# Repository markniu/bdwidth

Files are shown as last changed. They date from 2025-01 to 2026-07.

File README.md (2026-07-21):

# Filament monitor Sensor bdwidth

- Through the generated CSV file, we can intuitively see the diameter of the entire filament roll in the line chart in any position
- Improve print quality with automatic flow rate adjustment and stability with the runout/clog feature.

#### bdwidth sensor is an optical width and motion sensor for 3D printer.
I developed a unique algorithm that uses light diffraction to automatically compensate for filament shadows on the CCD sensor, even when the filament moves at different distances and angles, we still can get the right width.

  Just power it, then you can measure your filament motion&diameter.  



1. Flow compensation:  adjust the flow rate in real time

2. Jam/Runout: Pause the printer while jam or runout (laser optical tracking chip)
 
3. Width Accuracy: +/- 0.015mm  
 
4. Connection: USB or I2C, Low power 5V*49mA = 0.245W

5. No calibration required

6. firmware update from the usb (Only needs updating when we release a new bdwidth.hex)
   
7. No mechanical contact with the filament, no wear due to the use of optical components

[flow adjust](https://static.wixstatic.com/media/0d0edf_dd1a7dbbf0d7433387d54fea9a8ac6f3~mv2.jpg/v1/fill/w_1486,h_753,al_c,q_85,usm_0.66_1.00_0.01/0d0edf_dd1a7dbbf0d7433387d54fea9a8ac6f3~mv2.jpg)

[filament actual used](https://static.wixstatic.com/media/0d0edf_f45dd0ee38ac41dd8bb5706e1e4dc5ea~mv2.jpg/v1/fill/w_1440,h_753,al_c,q_85,usm_0.66_1.00_0.01/0d0edf_f45dd0ee38ac41dd8bb5706e1e4dc5ea~mv2.jpg)

[width chart](https://static.wixstatic.com/media/0d0edf_18b3c14cc95a42f3876c291456ff140b~mv2.jpg/v1/fill/w_1330,h_753,al_c,q_85,usm_0.66_1.00_0.01/0d0edf_18b3c14cc95a42f3876c291456ff140b~mv2.jpg)

## Quick start

#### 1.Plug the bdwidth sensor into the USB port or I2C port(it can be any two gpios) on the 3D printer mainboard 

#### 2.Install software module
```
cd  ~
git clone https://github.com/markniu/bdwidth.git
chmod 777 ~/bdwidth/klipper/install.sh
~/bdwidth/klipper/install.sh
```

#### 3.Configure Klipper

add the following section into your klipper config file,

here we connect the bdwidth to the usb port

```
[bdwidth fila_width_0]
port:usb
#   usb or i2c 
#i2c_software_scl_pin:PA8
#i2c_software_sda_pin:PA14
#   needed if the port is i2c
serial:/dev/serial/by-id/usb-1a86_USB_Serial-if00-port0
#serial:/dev/serial/by-path/YourByPathUUID
#   needed if the port is usb
# note: if you also have a bd_pressure , you must use  a serial: /dev/serial/by-path method.
# uncomment the above by-path line and replace the "YourByPathUUID" with the UUID for the bd_width. See the bd_pressure repository for instruction for bd_pressure. 
# It's best to start with both unplugged, then use command: ls /dev/serial/by-path and take note of the UUIDs with both unplugged.
# Repeat the command again after plugging in bd_width. Take note of the UUID for it, then again repeat for bd_pressure.

default_nominal_filament_diameter: 1.75 # (mm)
enable: all
#  disable or enable the sensor after power on.
#   the value should be one of width/motion/all/disable 
#   width(only enable the width function)
#   motion(only enable the motion function)
#   all(enable both the width and motion)
#   disable(disable both the width and motion)
min_diameter: 1.0
#   Minimal allowed diameter for flow rate adjust and runout.
max_diameter: 2.0
#   Maximum allowed diameter for flow rate adjust and runout.
#   The default is default_nominal_filament_diameter + max_difference.
extruder:extruder
runout_delay_length : 8.0  
#    (mm) increase this value if the print speed is high or with high flowrate 
#    else it may trigger the runout and pause
flowrate_adjust_length : 5  # (mm)
pause_on_runout: True
sample_time:2
#  in seconds, should be > 0.3s
sensor_to_nozzle_length: 750
#   The distance from sensor to the melting chamber/hot-end in
#   millimeters (mm). The filament between the sensor and the hot-end
#   will be treated as the default_nominal_filament_diameter. Host
#   module works with FIFO logic. It keeps each sensor value and
#   position in an array and POP them back in correct position. This
#   parameter must be provided.
#   how to measure:https://github.com/markniu/bdwidth/blob/main/doc/lengthToNozzle.jpg

logging: True
#   Out data to the file bdwidth.log.csv,
#   the data format: date time,diameter,total used filament,raw data of total used filament. 
#   for example:
#   7/12 23:20:18,1.764mm,1462.5mm,62594

debug_info: True
#   Output diameter to terminal/console and klipper.log 

```

### 4. Gcode for bdwidth:
```
SET_BDWIDTH NAME=xxx COMMAND=ENABLE  ;enable the bdwidth 
SET_BDWIDTH NAME=xxx COMMAND=DISABLE  ;disable the bdwidth 
SET_BDWIDTH NAME=xxx COMMAND=QUERY    ;read one data from bdwidth
```
note: the `xxx` is the name of bdwidth in the section [bdwidth xxx]
for example: [bdwidth fila_width_0] in the printer.cfg then we can run this command to enable it.
```
  SET_BDWIDTH NAME=fila_width_0 COMMAND=ENABLE
```

> The bdwidth is not enabled by default, we need to enable it with command, and Add the enable or disable command into the start G-code in the slicer.
> for example:SET_BDWIDTH NAME=fila_width_0 COMMAND=ENABLE

#### [Test Video1](https://www.youtube.com/watch?v=Cj5bzoDzowE)  , [Test Video2](https://www.youtube.com/watch?v=vu5LtXh5HZw) 
[Test Video3](https://www.tiktok.com/@plumpkatt1/video/7567149596976090381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)

## Community & Support
 
| Channel | Link |
|---|---|
| Discord | [discord.gg/z6ahddnGVU](https://discord.gg/z6ahddnGVU) |
| Facebook group | [facebook.com/groups/380795976169477](https://facebook.com/groups/380795976169477) |
| Where to buy | 🇺🇸 [fabreeko.com](https://fabreeko.com) <br> 🇺🇸 [west3d.com](https://west3d.com) <br> 🌏 [pandapi3d.com](https://pandapi3d.com) <br> 🇨🇳 [淘宝](https://shop62248922.taobao.com/) <br> 🇮🇹 [mabs3d.com](https://www.mabs3d.com/en/shop/products/bd-width-sensor) <br> 🇩🇰 [3do.dk](https://3do.dk/12-abl-probe) |

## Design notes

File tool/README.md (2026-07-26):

ccd_flash.exe is a combined Windows tool that serves two purposes:
### CCD Data Viewer  +  STM32 Firmware Flasher

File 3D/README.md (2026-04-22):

### [Disassemble and Assemble Video](https://youtu.be/USu0WTB1Q10?si=Ljlww_SiTaMyBVeS)

Note: The black filament should be used for printing the case.

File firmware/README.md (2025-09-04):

#Firmware Download into bdwidth sensor

1. Press and Hold on the boot button on the bdwidth sensor
2. Power on the bdwidth sensor with usb cable
3. Release the boot button
4. Open the STM32CubeProgrammer.exe
5. Choose the UART port and click connect button in the STM32CubeProgrammer
6. Open the firmware file for example: bdwidth_v1.1.hex --> Click Download
7. Finish

Video: https://youtu.be/c74Q1chOo8M

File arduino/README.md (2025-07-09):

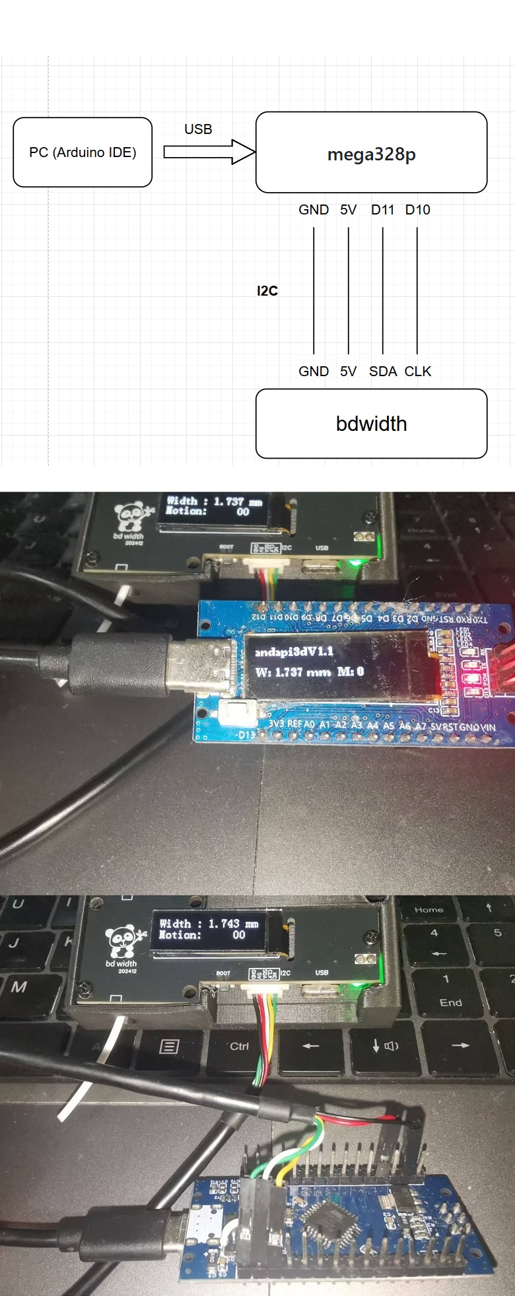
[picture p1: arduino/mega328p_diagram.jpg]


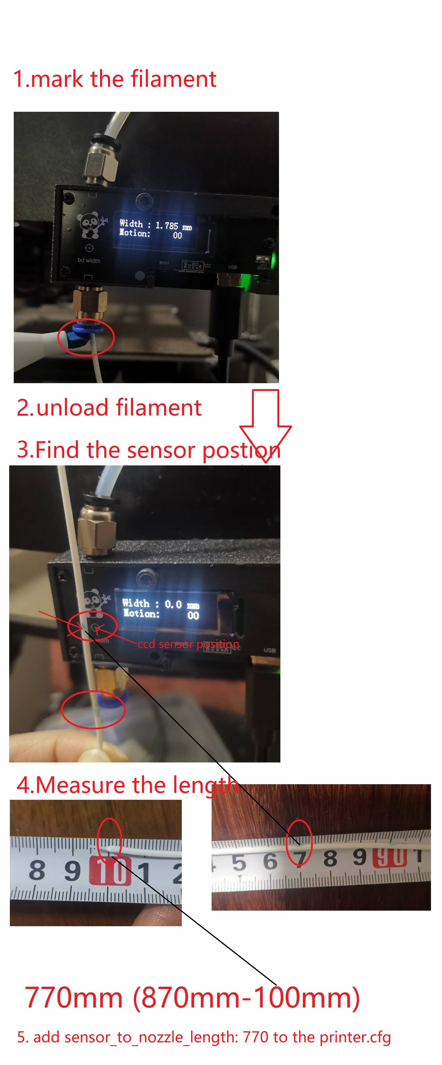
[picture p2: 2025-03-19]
doc/lengthToNozzle.jpg

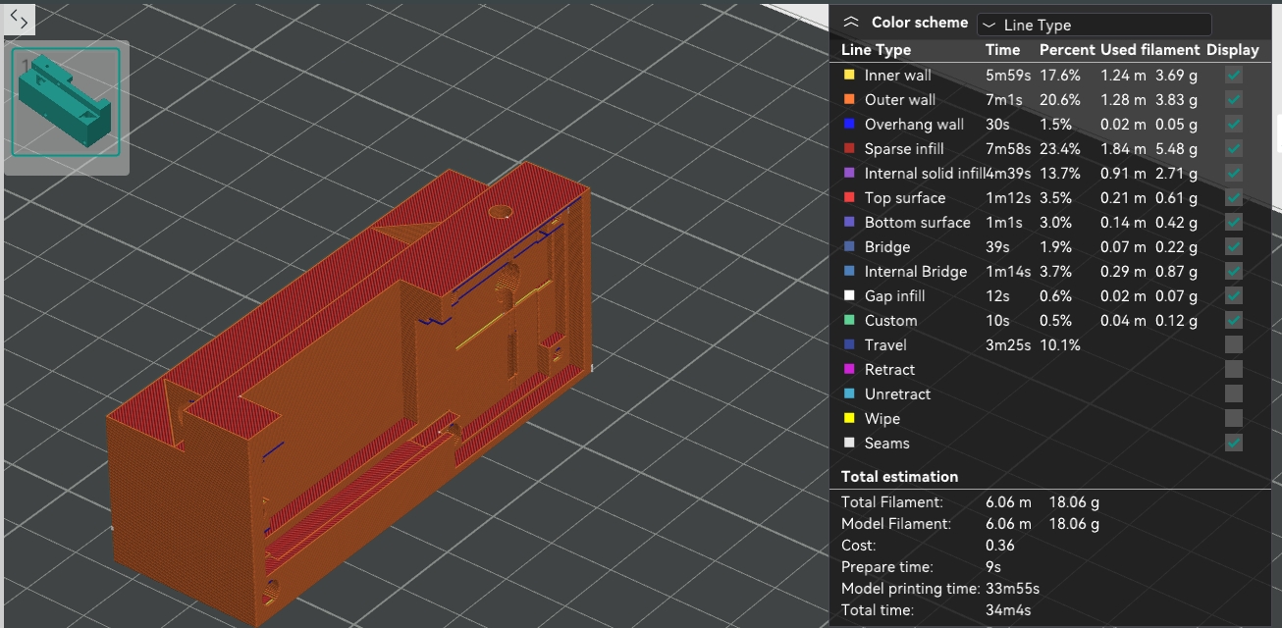
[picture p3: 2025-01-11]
3D/slice.jpg

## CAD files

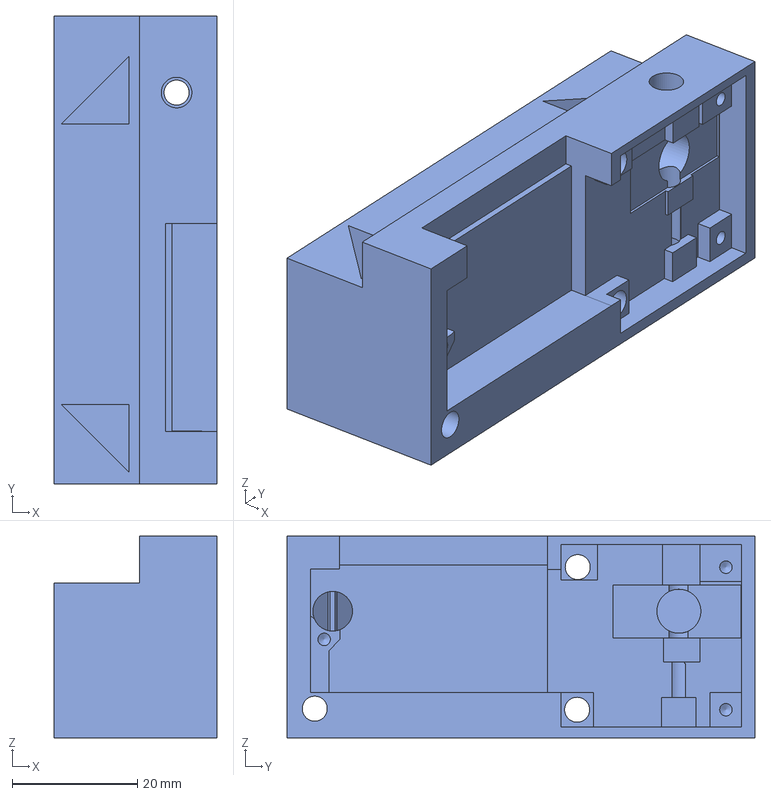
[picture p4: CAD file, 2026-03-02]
3D/bdwidth4mm.step
26.0 x 74.9 x 32.2 mm

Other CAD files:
3D/bdwidth4mm.stl

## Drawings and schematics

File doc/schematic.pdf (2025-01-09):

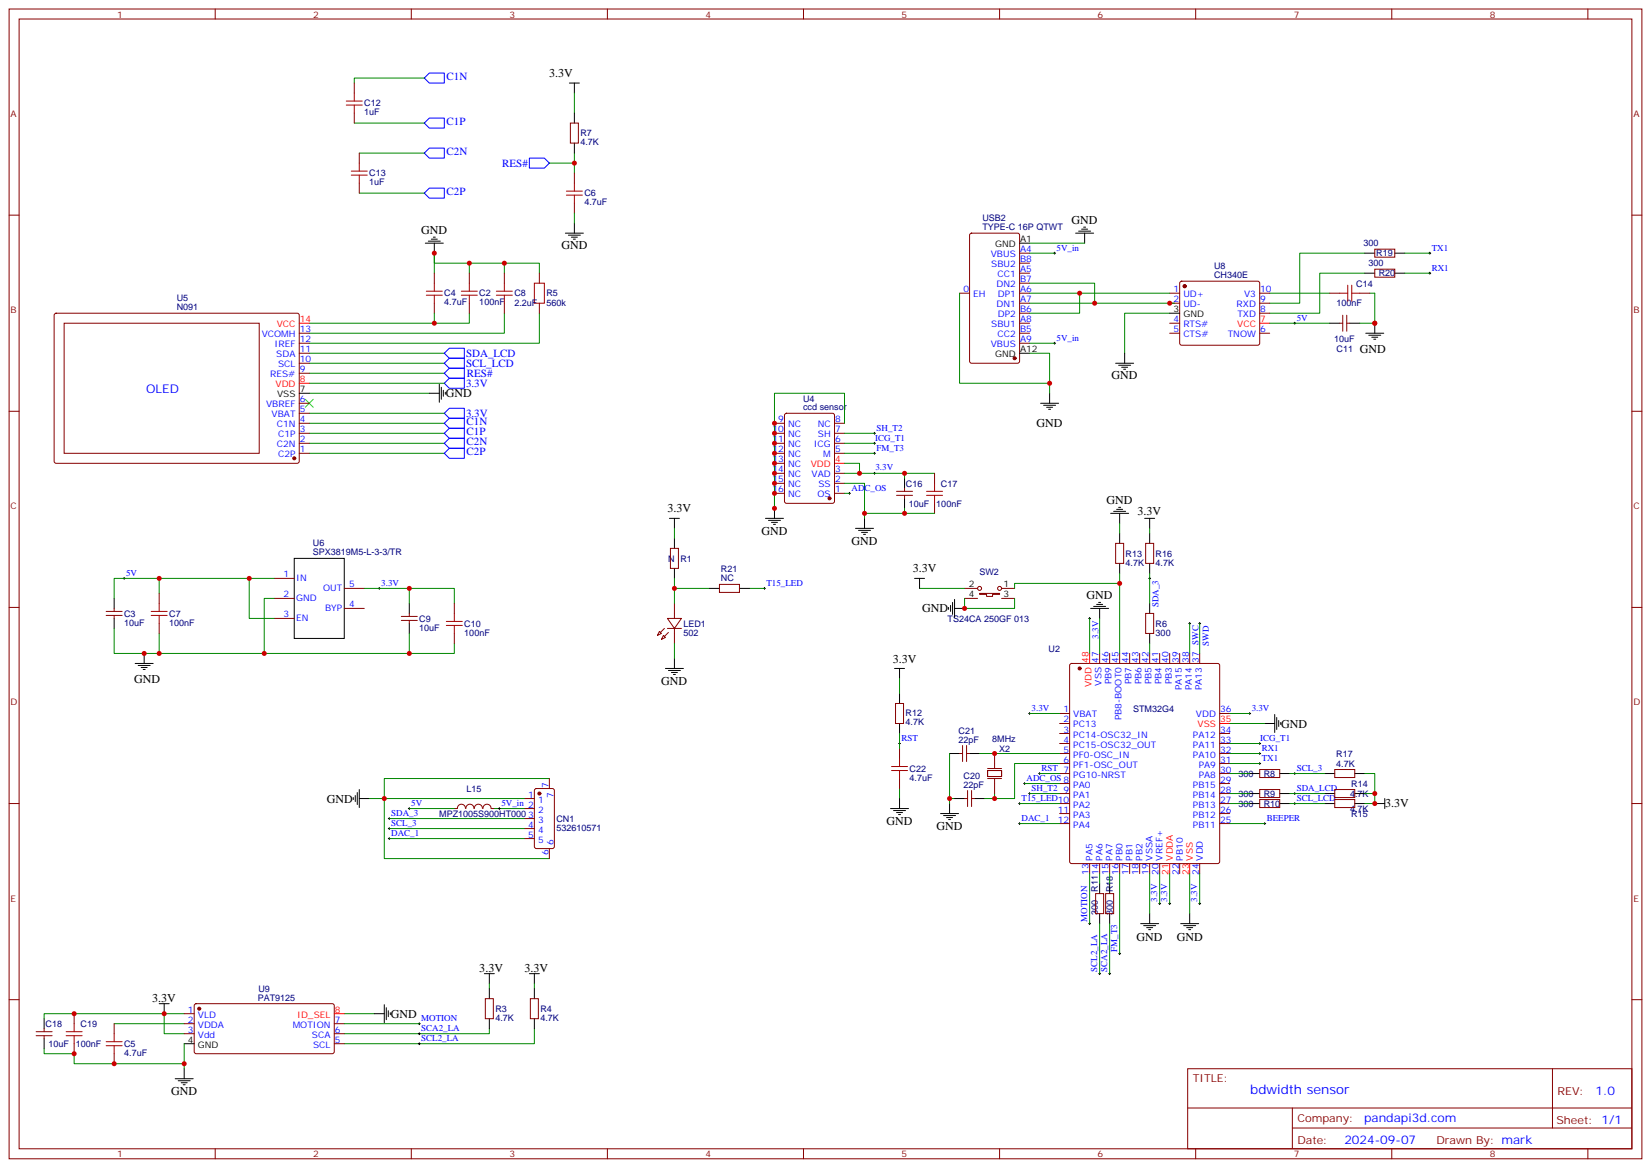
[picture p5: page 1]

SCL 10 SDA 11 IREF 12 VCOMH 13 VCC 14

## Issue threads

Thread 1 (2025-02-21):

BDWIDTH case

CBoismenu, 2025-02-21:
Recently purchased one of your BDWIDTH sensors.

Looking at the STL for the case I see that it's not made to use those pneumatic fittings like the ones you have in your assembly video.

Any possibility of adding the stl for that type of housing.

Thanks in advance for your help.

markniu, 2025-02-22:
Oh, forget to update that stl.  I just updated it:  https://github.com/markniu/bdwidth/tree/main/stl

CBoismenu, 2025-02-22:
Thank you thta is exactly what I waa looking for.

Closed 2025-02-22.

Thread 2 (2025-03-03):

Feature request: Kalico support

SinisterRj, 2025-03-03:
The plugin doesn't work with Kalico. The first error is related to the "runout_helper" function on Kalico require more arguments than the Klipper original one.

markniu, 2025-03-05:
Thanks for feedback this, and I am trying to use the Kalico, but meet some error like not support can bus `ModuleNotFoundError: No module named 'can'`

SinisterRj, 2025-03-10:
It supports can bus... I don't know if they changed the module name, but I have two printers with can tool heads running with Kalico.

SinisterRj, 2025-03-11:
Maybe the Venv where you are testing is broken. Try a fresh install or `
~/klippy-env/bin/pip install -r ~/klipper/scripts/klippy-requirements.txt`

markniu, 2025-03-13:
I have updated the code that can support Kalico in my printer, you can try it.

SinisterRj, 2025-03-21:
Thanks my friend. I installed in my printer and no more errors until now. But I was unable to do a test print because my printer has another problems right now. But I think we can close the issue and if I found another problem I will raise a new one. Thanks.

Closed 2025-03-21.

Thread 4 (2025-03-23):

Unhandled exception during run

CBoismenu, 2025-03-23:
Since the latest Klipper Update I'm getting an "Unhandled exception during run" error message anytime I enable the section for the bdwidth sensor (USB Mode).

It was working fine before the upgrade.

Same situation on two different printer.

If I disable the bdwith section everything works as expected.

markniu, 2025-03-24:
could you send me or attach the klippy.log file?

CBoismenu, 2025-03-24:
Tried the new code same result.

[klippy.log](https://github.com/user-attachments/files/19437194/klippy.log)

klippy log included.

markniu, 2025-03-25:
there is no other error except the MCU is shutdown, maybe you need to repower the board.
```
MCU error during connect
Traceback (most recent call last):
  File "/home/pi/klipper/klippy/klippy.py", line 135, in _connect
    cb()
  File "/home/pi/klipper/klippy/mcu.py", line 743, in _connect
    config_params = self._send_get_config()
  File "/home/pi/klipper/klippy/mcu.py", line 729, in _send_get_config
    raise error("Can not update MCU '%s' config as it is shutdown" % (
mcu.error: Can not update MCU 'mcu' config as it is shutdown
Can not update MCU 'mcu' config as it is shutdown
```

CBoismenu, 2025-03-25:
Thanks for getting back to me.

What do you mean by repower the board are you talking about the sensor board (disconnect and reconnect) or are you talking about another board.

Also, when they talk about MCU, are they talking about the raspberry py set up as a secondary MCU:

[mcu host] (raspberry pi)

or are they talking about another one, I also have the following boards set-up as MCU's:

[mcu] (Octopus)

[mcu U2C]

[mcu EBBCan] (BTT EBB2209 Canbus)

If that helps, the only difference between the error message being generated or not, is enabling or disabling de [bdwidth] section in the klipper printer.cfg file. But in both cases the sensor is plugged in and displaying information.

As I said in the original message the sensor was working as expected on both my printers before the software upgrades, leading me to believe that something as changed in one of the files and that is what is causing the error message to be generated.

If use the ls /dev/serial/by-id/* command in the console, I do see the serial address of the bdwidth sensor board:
/dev/serial/by-id/usb-1a86_USB_Serial-if00-port0

Let me know if you need anything else, i'll be more than happy to help.

Again thanks for you help.

markniu, 2025-03-25:
from that log the host can't connect to the MCU, and no other error information like the "Unhandled exception during run", from my experience is need to reset the MCU with hardware like repower the whole printer.  you can try that and send me the klippy.log again.

markniu, 2025-03-25:
what's your python version?

CBoismenu, 2025-03-25:
Both printers have Python version 3.9.2

For one of my printers I had an image of an earlier version of klipper and with that image the sensor works without any problems.

CBoismenu, 2025-03-26:
Just rolled back the klipper version, on my other printer, using KIAUH and with a previous version of klipper the bdwidth sensor works.

So definitely the klipper upgrade is what caused the filament width sensor to malfunction.

CBoismenu, 2025-03-28:
Hi,
You're update to the bdwidth.py fixed the issue.
Thanks for your work.
I'm realy enjoying the sensor it as improved my prints.

Closed 2025-04-08.

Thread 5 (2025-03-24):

Abrupt variations and inconsistent reading

SinisterRj, 2025-03-24:
Hello,

I'm having some inconsistent readings, with huge changes between one reading to another:

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

Maybe it is because my temporary installation (with the sensor literally hanged by the reverse bowden), but I was wondering if the firmware just make one measurement on the sampling rate defined in the config file, or if it make more samples and return an average of these measurements to Klipper in the defined interval. But, in fact the corrections are getting my prints worse:

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

(same filament, same printer, same STL, bottom without sensor, top with the sensor)

Do you have any Discord Server? It would be easier to talk there.

markniu, 2025-03-25:
Did you disassemble the sensor before? If so, it is recommended to clean the glass surface of the sensor

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

I just create a discord
https://discord.gg/bXxKAxBC

markniu, 2025-03-25:
there is no need to average of measurements from the klipper as the measurement is very stable normally.

markniu, 2025-03-25:
I will release a soft tool for check the sensor, like the installation problem or if it is need to clean the glass.

Closed 2025-04-08.

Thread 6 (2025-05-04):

Feature request: Turn off oled screen

spaivaras, 2025-05-04:
As firmware is not open source, would like to request a feature to shutdown the OLED screen if for example no filament movement is detected for certain amount of time (like 60s or even better configurable). This should save from OLED burn in

markniu, 2025-05-19:
Thanks for that suggestion, now I just updated the new firmware that can support auto on/off the OLED.

It uses the motion sensor to determine whether to turn the OLED on or off.
turn off:
   it will turn off the OLED after 10 minutes if there is no filament motion detected.
turn on:
   it will turn on the OLED immediately if motion is detected

spaivaras, 2025-05-19:
This is awesome news!!, Thank you!

spaivaras, 2025-05-19:
Just updated my bdwidth with 1.1. Works like a charm! Now it will prolong the life of screen when the print is done in a middle of night for example.

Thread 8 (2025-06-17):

Stiffer filament gets stuck inside the filament port when inserting

sshantt, 2025-06-17:
When trying to pass through stiffer filament like PPA-CF and PPS-CF through the hole, it tends to get stuck. The 3D printed part needs to be redesigned. Also there is quite a bit of friction with CF and GF filament because it rubs against a lot of the 3D printed part when passing through. There should be ptfe tube all the way to the sensors from both sides.

Please share a step file so I can implement the fix and issue a PR

markniu, 2025-06-17:
Thanks！  This version was designed with Tinkercad, which can only export in STL file. I am redesigning it with Onshape that  can export to STEP.

markniu, 2025-06-21:
Hello,  the step file was uploaded : https://github.com/markniu/bdwidth/tree/main/3D

markniu, 2025-09-01:
Note: The matte black PLA must be used for printing the case.

Closed 2025-09-04.

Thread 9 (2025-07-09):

Kailco compatibility?

Nathan22211, 2025-07-09:
Kailco's a klipper fork with a lot of features the main Klipper dev wouldn't add. Only thing is, it's based on Klipper 0.12.0, v0.13.0 of mainline broke a lot of extras from what I hear.

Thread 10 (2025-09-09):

Multiple Identical Serial Devices & Soultion for MCU Connection Issues

xboxhacker, 2025-09-09:
I recently got a bdwidth for my Klipper TronXY Veho600 printer. I instantly ran into issues with MCU connection problems. After spending 2 full days working it out, it is now working fine. I want to put this here in case someone else is having the same MCU connection problems I had.

### Hardware:

- TronXY stm32f446
- BTT Pi 1.2
- bdwidth

It would seem my main board uses the same CH340 as the bdwidth. This caused a conflict when connecting to the MCU. Vendor 1a86, same product, no unique serial.

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

Result: using `/dev/serial/by-id/usb-1a86_USB_Serial-if00-port0` is ambiguous and will sometimes point to the MCU, other times to the sensor, causing read errors.

_NOTE: I 100% do not know what I am doing, but I dug and dug to work this solution out. There may be far better ways to do this, but it works for me._

---

### 1. Identify Your Devices

Plug in both USB-serial devices (e.g., printer board and filament sensor).

List all USB serial devices:

```bash
ls -l /dev/ttyUSB*
ls -l /dev/serial/by-path
```

Unplug one device to see which `/dev/ttyUSB*` disappears—this helps you match each device to its function.

---

### 2. Get Each Device's Physical USB Path

For each device, run:

```bash
udevadm info -q property -n /dev/ttyUSB0 | grep ^ID_PATH=
udevadm info -q property -n /dev/ttyUSB1 | grep ^ID_PATH=
```

Example output:

```
ID_PATH=platform-5101400.usb-usb-0:1:1.0
ID_PATH=platform-5200400.usb-usb-0:1:1.0
```

---

### 3. Create a udev Rules File

Create `/etc/udev/rules.d/99-serial-stable-names.rules` with your favorite editor.

```Nano
sudo nano /etc/udev/rules.d/99-serial-stable-names.rules
```

**Paste this into Nano:**
```udev
# Replace ID_PATH values with those from your system!
SUBSYSTEM=="tty", ENV{ID_PATH}=="<YOUR PATH HERE>", SYMLINK+="mcu"
SUBSYSTEM=="tty", ENV{ID_PATH}=="<YOUR PATH HERE>", SYMLINK+="bdwidth"
```
Save the new file with `CTRL + X`

---

### 4. Reload udev and Replug Devices

```bash
sudo udevadm control --reload-rules
sudo udevadm trigger -s tty
```

Check the new symlinks:

```bash
ls -l /dev/mcu /dev/bdwidth
```

---

### 5. Update Your Klipper `printer.cfg`

```ini
[mcu]
serial: /dev/mcu
restart_method: command

[bdwidth]
port: usb
serial: /dev/bdwidth
extruder: extruder
enable: all
<rest of the config from the git>
```

---

### 6. Troubleshooting

- If `/dev/mcu` or `/dev/bdwidth` don’t appear, double-check the **ID_PATH** values and your rules file for typos.
- Reload rules and replug both devices.
- Use `sudo udevadm test $(udevadm info -q path -n /dev/ttyUSB0)` to debug rule application.
- Never move the device to a different USB port, or you’ll need to redo the steps above.

---

## Bonus: Use `by-path` Directly (Quick Hack)

You can also use `/dev/serial/by-path/...` in your config if you don't want to set up custom names.

Example:

```printer.cfg
[mcu]
serial: /dev/serial/by-path/platform-5101400.usb-usb-0:1:1.0
restart_method: command
```
_Untested by me..._

markniu, 2025-09-10:
This is very useful. Thanks for sharing!

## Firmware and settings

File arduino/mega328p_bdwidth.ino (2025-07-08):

// Ardunio Nano, mega328p
// read data from bdwith sensor via i2c port.
// software i2c, so we can use any 2 free gpio for the SDA and SCL.

#include <Arduino.h>
#include <U8g2lib.h>
#ifdef U8X8_HAVE_HW_SPI
#include <SPI.h>
#endif
#ifdef U8X8_HAVE_HW_I2C
#include <Wire.h>
#endif

#define SDA_PIN 11
#define SCL_PIN 10

#define sensor_addr 3
#define version_addr 0x06
#define width_addr 0x16

char tmp_1[50];

U8G2_SSD1306_128X32_UNIVISION_F_SW_I2C u8g2(U8G2_R0, /* clock=*/ SCL, /* data=*/ SDA, /* reset=*/ U8X8_PIN_NONE);  


void i2c_init() {
  pinMode(SDA_PIN, INPUT_PULLUP);
 // pinMode(SCL_PIN, INPUT_PULLUP);
  pinMode(SCL_PIN, OUTPUT);
  //digitalWrite(SDA_PIN, HIGH);
  //digitalWrite(SCL_PIN, HIGH);
}

void i2c_start() {
  pinMode(SDA_PIN, INPUT_PULLUP);
  digitalWrite(SCL_PIN, HIGH);
  delayMicroseconds(50);

  pinMode(SDA_PIN, OUTPUT); 
  digitalWrite(SDA_PIN, LOW);
  delayMicroseconds(5);
  digitalWrite(SCL_PIN, LOW);
  delayMicroseconds(5);
}

void i2c_stop() {
  pinMode(SDA_PIN, OUTPUT); 
  digitalWrite(SDA_PIN, LOW);
  delayMicroseconds(5);
  digitalWrite(SCL_PIN, HIGH);
  delayMicroseconds(5);
  //digitalWrite(SDA_PIN, HIGH);
  pinMode(SDA_PIN, INPUT_PULLUP);
  delayMicroseconds(5);
}

bool i2c_write(byte data) {
  for (int i = 7; i >= 0; i--) {
   // digitalWrite(SDA_PIN, (data & (1 << i)) ? HIGH : LOW);
    if(data & (1 << i))
        pinMode(SDA_PIN, INPUT_PULLUP);
    else{
        pinMode(SDA_PIN, OUTPUT);
        digitalWrite(SDA_PIN, LOW); 
    }  
    delayMicroseconds(5);
    digitalWrite(SCL_PIN, HIGH);
    delayMicroseconds(5);
    digitalWrite(SCL_PIN, LOW);
    delayMicroseconds(5);
  }
  
  // check ACK
  pinMode(SDA_PIN, INPUT_PULLUP);
  digitalWrite(SCL_PIN, HIGH);
  delayMicroseconds(5);
  bool ack = digitalRead(SDA_PIN) == LOW;
  digitalWrite(SCL_PIN, LOW);
  //pinMode(SDA_PIN, OUTPUT);
  pinMode(SDA_PIN, INPUT_PULLUP);
  return ack;
}

byte i2c_read(bool ack) {
  byte data = 0;
  pinMode(SDA_PIN, INPUT_PULLUP);
  delayMicroseconds(5);
  for (int i = 7; i >= 0; i--) {
    digitalWrite(SCL_PIN, HIGH);
    delayMicroseconds(5);
    if (digitalRead(SDA_PIN)) data |= (1 << i);
    digitalWrite(SCL_PIN, LOW);
    delayMicroseconds(5);
  }
  
  // send ACK/NACK
  
  //digitalWrite(SDA_PIN, ack ? LOW : HIGH);
   if(!ack)
        pinMode(SDA_PIN, INPUT_PULLUP);
    else{
        pinMode(SDA_PIN, OUTPUT);
        digitalWrite(SDA_PIN, LOW); 
    } 

  digitalWrite(SCL_PIN, HIGH);
  delayMicroseconds(5);
  digitalWrite(SCL_PIN, LOW);
  pinMode(SDA_PIN, INPUT_PULLUP);
  
  return data;
}

byte readI2CRegister(byte deviceAddr, byte regAddr,uint8_t *buf, uint8_t len) {

  i2c_start();

  i2c_write(deviceAddr<<1); // write mode
  i2c_write(regAddr);
  i2c_start();
  i2c_write((deviceAddr<<1)|1); // read mode
  uint8_t i=0;
  for(i=0; i<len-1; i++) {
    buf[i] = i2c_read(true); // send ACK
  }
  buf[i] = i2c_read(false);  // don't send ACK for the last byte.

  i2c_stop();
  return 0;
}
void setup(void) {
  u8g2.begin();
  u8g2.clearBuffer();          // clear the internal memory
  i2c_init();
}

void loop(void) {
  uint8_t data[20];     
  u8g2.clearBuffer(); 
  u8g2.setFont(u8g2_font_ncenB08_tr); // choose a suitable font

  
  // read bdwidth version
  readI2CRegister(sensor_addr, version_addr,data,15);
  sprintf(tmp_1,"%s\n",data);
  u8g2.drawStr(0,10,tmp_1);
  // read width and motion data
  readI2CRegister(sensor_addr, width_addr,data,4);
 unsigned long width = ((data[1] << 8) + data[0])&0xffff;
  int motion = ((data[3] << 8) + data[2])&0xffff;
  //sprintf(tmp_1,"W:%d,M:%d\n",width*525,motion);
  width = width*525;
	//sprintf(tmp_1,"W: %d.%d%d%d,M:%d",width/100000,(width%100000)/10000,(width%10000)/1000,(width%1000)/100,motion);
  sprintf(tmp_1,"W: %d.",width/100000 );
  sprintf(tmp_1+strlen(tmp_1),"%d",(width%100000)/10000);
  sprintf(tmp_1+strlen(tmp_1),"%d",(width%10000)/1000);
  sprintf(tmp_1+strlen(tmp_1),"%d mm",(width%1000)/100);
  sprintf(tmp_1+strlen(tmp_1),"  M: %d",motion);
  u8g2.drawStr(0,30,tmp_1);
    
  
  delay(1000);  
  u8g2.sendBuffer();


}

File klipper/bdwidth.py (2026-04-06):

import logging
import math
import statistics
import serial
import serial.tools.list_ports
import os
import time


from . import bus
from . import filament_switch_sensor


# --- USB Auto-detection helpers ---

# Version strings returned by 'G00;' / 'V;':
#   bdwidth    -> pandapi3dV1  (capital V)
#   bdpressure -> pandapi3dv1  (lowercase v)
# We match on 'pandapi3dV' (capital V, case-sensitive) to identify bdwidth.
BDWIDTH_BAUD = 500000
BDWIDTH_VERSION_MARKER = 'pandapi3dV'   # capital V  = bdwidth

# CH340/CH341 USB-serial chips  vendor ID 1A86 (QinHeng Electronics)
CH340_VID = 0x1A86
CH340_KEYWORDS = ('ch340', 'ch341', '1a86', 'qinheng')


def _list_all_serial_ports():
    return [p.device for p in serial.tools.list_ports.comports()]


def _list_ch340_ports():
    found = set()

    # --- Methods 1 & 2: pyserial comports() ---
    for p in serial.tools.list_ports.comports():
        vid = getattr(p, 'vid', None)
        desc = (p.description or '').lower()
        hwid = (p.hwid or '').lower()
        if vid == CH340_VID:
            found.add(p.device)
            continue
        if any(k in desc or k in hwid for k in CH340_KEYWORDS):
            found.add(p.device)

    # --- Method 3: /dev/serial/by-id/ symlink scan ---
    by_id_dir = '/dev/serial/by-id'
    if os.path.isdir(by_id_dir):
        for name in os.listdir(by_id_dir):
            if any(k in name.lower() for k in CH340_KEYWORDS):
                symlink = os.path.join(by_id_dir, name)
                try:
                    real = os.path.realpath(symlink)
                    found.add(real)
                    logging.info(
                        "bdwidth auto-detect: found CH340 via by-id: %s -> %s" % (name, real)
                    )
                except Exception:
                    pass

    return list(found)


def _probe_port_for_bdwidth(port):
    ser = None
    try:
        ser = serial.Serial(port, BDWIDTH_BAUD, timeout=0.6)
        time.sleep(0.2)
        ser.reset_input_buffer()
        ser.reset_output_buffer()

        ser.write(b'G00;\n')
        line = ser.readline()
        text = line.decode('utf-8', errors='ignore').strip()
        logging.info(
            "bdwidth auto-detect: port=%s baud=%d cmd='G00;' response=%r"
            % (port, BDWIDTH_BAUD, text)
        )
        ser.close()
        # Capital V = bdwidth; lowercase v = bdpressure
        if BDWIDTH_VERSION_MARKER in text:
            return port, text

    except Exception as e:
        logging.warning("bdwidth auto-detect: error probing %s at %d baud: %s"
                        % (port, BDWIDTH_BAUD, e))
        if ser is not None:
            try:
                ser.close()
            except Exception:
                pass
    return port, None


def auto_detect_bdwidth_port():
    # --- Pass 1: CH340-labelled ports ---
    ch340_ports = _list_ch340_ports()
    logging.info("bdwidth auto-detect: CH340 candidates = %s" % ch340_ports)
    for port in ch340_ports:
        matched_port, resp = _probe_port_for_bdwidth(port)
        if resp is not None:
            logging.info(
                "bdwidth auto-detect: found BDWidth on %s (version: %r)" % (matched_port, resp)
            )
            return matched_port

    # --- Pass 2: all serial ports (fallback) ---
    all_ports = _list_all_serial_ports()
    # skip ports we already tried
    remaining = [p for p in all_ports if p not in ch340_ports]
    logging.info(
        "bdwidth auto-detect: CH340 pass found nothing; "
        "trying remaining ports: %s" % remaining
    )
    for port in remaining:
        matched_port, resp = _probe_port_for_bdwidth(port)
        if resp is not None:
            logging.info(
                "bdwidth auto-detect: found BDWidth on %s (version: %r)" % (matched_port, resp)
            )
            return matched_port

    logging.warning(
        "bdwidth auto-detect: BDWidth not found. "
        "Probed CH340=%s + fallback=%s. "
        "Check klippy.log for per-port responses." % (ch340_ports, remaining)
    )
    return None


BDWIDTH_CHIP_ADDR = 3
BDWIDTH_I2C_SPEED = 100000
BDWIDTH_REGS = {
     '_version' : 0x6,
     '_measure_data' : 0x16

}

class BDWidthMotionSensor:
    def __init__(self, config):
        self.printer = config.get_printer()
        self.reactor = self.printer.get_reactor()
        self.port = config.get("port")

        # if config.get("resistance1", None) is None:
        if "i2c" in self.port:  
            self.i2c = bus.MCU_I2C_from_config(config, BDWIDTH_CHIP_ADDR, BDWIDTH_I2C_SPEED)
        elif "usb" in self.port:
            baudrate = 500000
            configured_serial = config.get("serial", None)
            if configured_serial is None or configured_serial.strip().lower() == "auto":
                # Auto-detect: scan CH340 ports and identify BDWidth by baud rate (500000)
                usb_port = auto_detect_bdwidth_port()
                if usb_port is None:
                    raise config.error(
                        "BDWidthMotionSensor: could not auto-detect USB port. "
                        "No CH340 device responded at 500000 baud. "
                        "Set 'serial' explicitly in the config if auto-detection fails."
                    )
                logging.info("BDWidthMotionSensor: using auto-detected port %s" % usb_port)
            else:
                usb_port = configured_serial
            self.usb_port = usb_port
            self.usb = serial.Serial(self.usb_port, baudrate, timeout=1)
        self.gcode = self.printer.lookup_object('gcode')
        self.extruder_name = config.get('extruder')
        self.check_on_print_start = config.getboolean(
            "check_on_print_start", False)
        try: 
            self.runout_helper = filament_switch_sensor.RunoutHelper(config)
        except Exception as e:
            self.runout_helper = filament_switch_sensor.RunoutHelper(config,self)
        self.get_status = self.runout_helper.get_status
        self.extruder = None
        self.estimated_print_time = None
        # Initialise internal state
        self.filament_runout_pos = 0.0
        self.filament_present = True
        
        self.nominal_filament_dia = config.getfloat(
            'default_nominal_filament_diameter', above=1.0)
        self.sensor_to_nozzle_length = config.getfloat('sensor_to_nozzle_length', above=0.)
   
        self.runout_delay_length = config.getfloat('runout_delay_length', 7., above=0.)
        self.tolerance_count = config.getfloat('tolerance_count', 2, above=1)

        self.flowrate_adjust_length = config.getfloat('flowrate_adjust_length', 5., above=1.)
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

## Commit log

2024-12-13 support i2c
2025-01-09 add schematic and firmware
2025-01-11 update the stl of shell
    [case.stl, shell.stl]
2025-02-22 update the stl file
    [case_pneumatic.stl, case_without_pneumatic.stl]
2025-03-13 support kalico klipper
2025-03-27 sync code from klipper about switch sensor
2025-06-09 fix the a bug that cann't be enabled after disable
    [case_0508.stl]
2025-06-10 Compatible with older versions of Klipper.
2025-06-21 update the case 3D file, stl, step
    [bdwidth202506.step, bdwidth202506.stl, case_0508.stl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]
2025-06-28 1. add new 3D file for 1 to 4mm filament; 2. fix a bug for 3mm filament measure
    [bdwidth202506.step, bdwidth202506.stl, bdwidth4mm.step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]
2025-07-03 add arduino code for reading data from bdwidth
2025-08-28 add tolerance_count to reduce the pause
    [bdwidth.py]
2025-09-12 support multiple BDwidth sensor work at the printere same printer
2026-02-23 update the firmware, optimize light noise which caused by the printed shell with different filament
2026-03-02 update the case 3d file
    [bdwidth4mm.step, bdwidth4mm.stl]
